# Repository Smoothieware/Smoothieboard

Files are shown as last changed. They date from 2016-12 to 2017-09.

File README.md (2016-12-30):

Smoothieboard
=============

Smoothieboard is a free, open source, high performance and modular G-code interpreter and CNC controller for the LPC17xx micro-controller (32-bit ARM Cortex-M3).

The current BoM (Bill of Materials) can be found at https://docs.google.com/spreadsheet/ccc?key=0Api7_ZbfikkKdGRDblUwMDFWcm1CT2M2bENkQWpZZ0E&usp=drive_web#gid=0

A separate list is maintained for the connectors at https://docs.google.com/spreadsheets/d/1bT7xw4z405cyhR7MyXegm4-C2oinxpVefuf3KV13v_A/edit#gid=0

Licensed under CERN OHL v.1.2 or later http://ohwr.org/cernohl
No warranty is provided for this documentation implied or otherwise.

The policy regarding third party "clones" and "derivatives" of Smoothieboard is found at http://smoothieware.org/policy

This documentation is hosted at http://github.com/Smoothieware/Smoothieboard

Firmware is found at http://github.com/Smoothieware/Smoothieware

Documentation of use is hosted on a wiki at http://smoothieware.org

For more info or to let us know what you are doing with Smoothie email wolf.arthur@gmail.com
or join the Smoothie community on IRC Freenode in #smoothieware http://smoothieware.org/irc

Smoothieware is a certified open source hardware project (UID FR000001).

Smoothieboard, and Smoothieware, and the Smoothie-namespace are all trademarks of The Smoothie Project.
The hardware and software of The Smoothie Project are licensed under the CERN OHL v1.2 or later and GPL v3 or later licensing agreements respectively.
Copyright 2011-2016 by Arthur Wolf and Mark Cooper

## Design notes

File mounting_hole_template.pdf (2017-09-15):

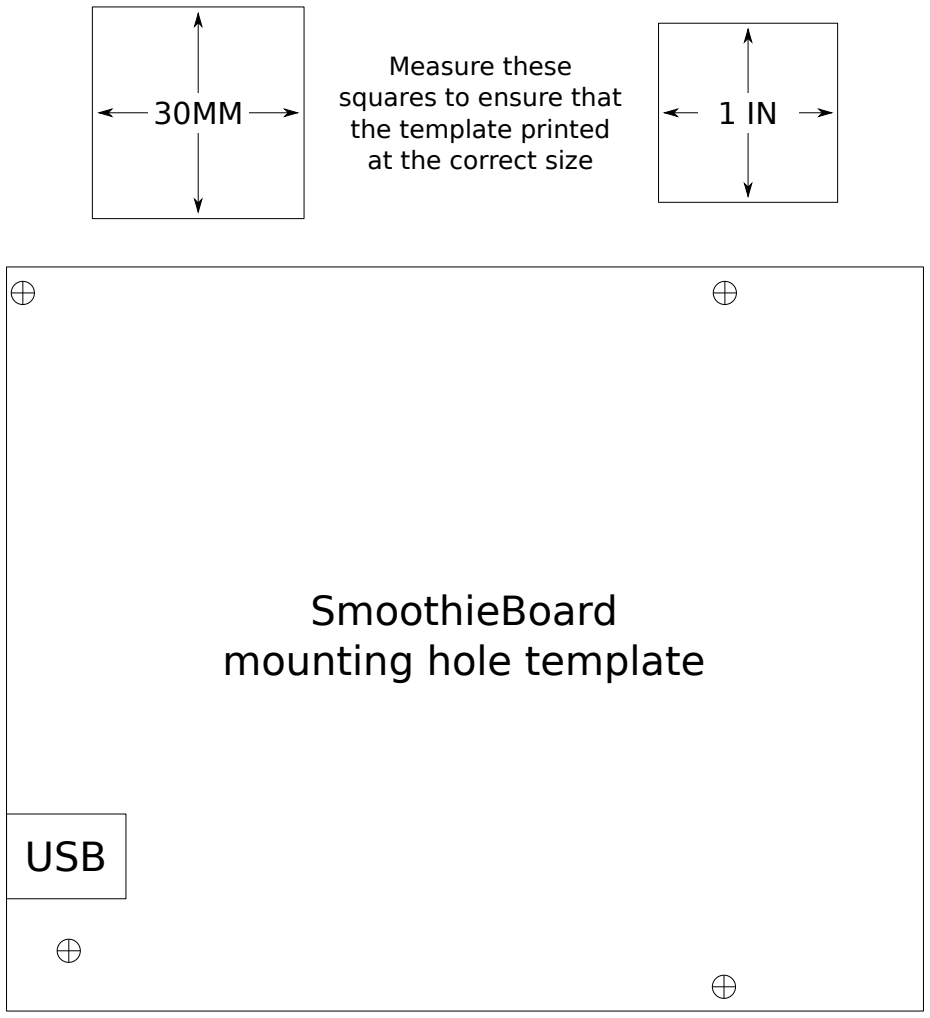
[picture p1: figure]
USB; SmoothieBoard mounting hole template; Measure these squares to ensure that the template printed at the correct size

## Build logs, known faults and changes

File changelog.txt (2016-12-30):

Smoothieboard Change Log

Smoothieboard v1.1 (2016/10)
 - upgraded stepper drivers to A5984 drivers with 32x microstepping
 - added a solder jumper (JP36) for MS3 on new A5984 drivers
 - changed the current limiting resistors (R78,R65-R68,R84-R85) for VBB powered LEDs to 8.2K
 - added an electrolytic capacitor (C84) to the 5V power system
 - moved the electrolytic capicitor (C63) for the 5x mosfet set and increased its footprint size
 - added flyback diodes (D7-D9) to small mosfet outputs to protect from inductive loads like small fans
 - added Open Source Hardware logo with UID (FR000001)

Smoothieboard v1.0b (2015/04)
 - reworked silkscreen adding reference ids back in
 - moved VBB jumper for small mosfet pair to increase room around C63
 - corrected the polarity of the zener diode in the VBB reverse polarity protection circuit
 - moved 5v reg backflow protection diode from the 5V side to the VBB side of the vreg
 - broke out AVCC and AGND to header
 - added solder jumper to TH4 passives

Smoothieboard v1.0a (2015/01)
 - update by Mark Cooper (Logxen)
 - reworked silkscreen with more pin numbers and without reference ids
 - added GND pin to the RST/ISP header
 - modified sdcard SPI1 header to match the pinout of the SPI0 header

Smoothieboard v1.0 (2014/09)
 - update by Mark Cooper (Logxen) and Michael Moon (Triffid_Hunter)
 - fixed missing connection between GND and AGND in KS layout
 - improved silkscreen
 - other small changes

Smoothieboard KS (2013/10)
 - expansion of the Beta design to a 5 driver layout by Michael Moon (Triffid_Hunter) and Mark Cooper (Logxen)
 - added "mixed" mosfet pair of one large and one small fet
 - improved VBB reverse polarity protection circuit
 - added esd protection to endstop circuits
 - added footprint for optional 5v regulator
 - additional GND pins for various headers
 - other small changes
 - produced by cooperation between Uberclock, Robotseed, and the Smoothie community
 - kickstarter page: https://www.kickstarter.com/projects/logxen/smoothieboard-the-future-of-cnc-motion-control

Smoothieboard Beta (2013/01)
 - designed by Arthur Wolf (arthur-_) and Eric Sorenson (ravix)
 - the original Smoothieboard Beta was a 4 stepper driver design
 - first produced by TrinityLabs and later produced by Ipsofactio which eventually rebranded as Robotseed
 - wiki page: http://smoothieware.org/smoothieboard-beta

Smoothieboard on a breadboard (circa 2011-current)
 - core design by Arthur Wolf (arthur-_)
 - original application circuits ported from RAMPS with modifications for use with 3.3V i/o
 - many community members built their own Smoothieboards on breadboards before Smoothieboards were commercially available
 - Smoothieboards on breadboards continue to be built today by people who are designing new derivative boards
 - wiki page: http://smoothieware.org/smoothie-on-a-breadboard

Smoothieboard and Smoothieware are trademarks of The Smoothie Project.
The hardware and software of The Smoothie Project are licensed under the CERN OHL v1.2 or later and GPL v3 or later licensing agreements respectively.
Copyright 2011-2016 by Arthur Wolf and Mark Cooper

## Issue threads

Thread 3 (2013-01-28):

2x3 connectors for ribbon cables ( SPI port ).

arthurwolf, 2013-01-28:
Hi !

I bought a bunch of these : http://www.ebay.com/itm/330833147832?ssPageName=STRK:MEWNX:IT&_trksid=p3984.m1497.l2649
They work great for the 5th-stepper connector, but a few caps and resistors are in the way for the SPI port. Could we move them away a bit ? ( that's on the beta board I have, may be different on the current eagle files ).
The connectors are 15*9mm.

Thanks !

Closed 2016-10-20.

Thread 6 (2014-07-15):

Menu typesetting messed up issue

zebrajack, 2014-07-15:
hi,
We use st7565_glcd for menu display, and the resolution is 128*64.After tedious configuration , finally it works, but the menu typesetting is a big issue as the following:

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

As we can see the first row is right typesetting when it is intialized, but it will change from time to time, switch back and force from 3 rows.

Does anyone encounter the same issue? Any suggestion are welcome!

Regards!
Cheng

Closed 2016-10-20.

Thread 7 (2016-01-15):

Stuck thermistors

traverseda, 2016-01-15:
Not sure exactly what happened, but the smoothieboard released a big puff of smoke, and the thermistors *stuck*. At 22.3 and 17.7 respectively.

Thankfully we were doing maintenance, and it didn't light anything on fire.

Looks like it was the chip next to c41. I'm guessing a A4982SLPTR-T.

Rebooted and the thermistors unstuck. Still pretty unclear on exactly what happened. Best guess is that it shorted on *something*, but whatever it was we can't find it.

Anyway, it's worth noting that the thermistors can fail partially open.

Closed 2016-10-20.

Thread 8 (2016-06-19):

R78 is too small

Zaaphod, 2016-06-19:
This is just a suggestion for a minor improvement to smoothieboard.  I recently hooked up my smoothieboard to a 24V power supply and noticed immediately that the red VBB led was so bright I could hardly see the nearby green led's 1-4

R78 is too small in comparison to the other current limiting resistors.  This is the current limiting resistor on the VBB LED10.  It's 2.2Kohms, but even at 12V the LED is extremely bright in comparison to the other LEDs,  and at 24V it's extremely bright.  The 2.2K resistor on LED 10 would make it draw 4.6mA at 12V and 10mA at 24V,  this is completely out or range of the other LEDs that draw only 1.5mA with their 1K current limiting resistors and 3.3V sources.

I noticed that other LEDs powered by VBB such as  LED5 - LED8 on the output FETs are 5.6K.  This is more in range if VBB=12V as the LED would be limited to 1.8mA  however at 24V it would still be overpowering at 4mA.
I would suggest 6.8Kohm - 10Kohm resistors for R78, and R65-R68 This would provide 1.5ma (6.8K) to 1mA (10K) at 12V and 3.3mA(6.8k) to 2.2mA(10k) at 24V - keeping these much more in range with the other LEDs.  Since I personally prefer 24V I would lean toward 10K, however even with 6.8K it would be much more in range of the other LEDs

Another option would be to make R78 5.6K and keep R65-R68 as is at 5.6K but then also reduce the size R10-R13 to 500-820ohms, this would make the green led's a little brighter. I would leave R77 alone because it's fine the way it is and is already brighter than the green LEDs

I realize this is a minor detail, but smoothie should be as good as it can be, and it's also a simple change to make.. no changes need to be made other than to change the resistor values.

Just for reference, I'm using 1.8v for the LED voltage drop and the formula  I=V-1.8/R  I don't know the exact specification of the LED's used

logxen, 2016-06-26:
Yeah, this has actually been bothering me for quite a while. I should make all of the VBB based resistors match in the next board revision.

  Your suggestion of 10K is a nice compromise between the two standard voltages used. I want to avoid using that specific value though because it is potentially confusing. The value of 10K strongly implies that the part is a simple pull-up or pull-down. The nearest values in the 10% series are 8.2K and 12K. I think 8.2K would be a good choice. Any higher than 10K and I fear the VBB leds would appear visibly dim at 12V.

Zaaphod, 2016-06-26:
I don't see what difference it makes whether it is the same value as a pull-up resistor, it's obviously in series with the LED.  However 8.2K would be way more balanced than the 2.2K resistor that is in there and be a big improvement.   If you wanted to stay away from 10K, then perhaps go with 8.2K for VBB resistors then decrease the green LED resistors to maybe 680ohms to help brighten the green LEDs a little.

logxen, 2016-11-06:
Being addressed in v1.1

Closed 2016-11-06.

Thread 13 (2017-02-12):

version updates missing

analogmonster, 2017-02-12:
eagle files still say v1.0 in the bottom right on schematic page - see page 3 of pdf and eagle sch.  Also may I suggest v1.1 be added to all pages.  I was looking for D7/D8 on my v1.0b board until I realised there was a misprint within eagle and I was referring to the wrong schematic

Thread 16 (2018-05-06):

Schematic file

seaghdh, 2018-05-06:
The .sch file is damaged. I want a .sch schema file.

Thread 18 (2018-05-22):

Add dimensions?

myk3y, 2018-05-22:
Nice to see a printable template for the board - would it be possible to put the dimensions and mount points in x,y format on the pdf?

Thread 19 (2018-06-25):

missing images in documentation

Jorgininho, 2018-06-25:
Hello,
I'm trying to follow the documentation on install smoothie on a k40 bluebox, but the images are not present in the both page
http://smoothieware.org/blue-box-guide
and
http://smoothieware.org/bluebox-guide

I remember there were usefull info on the type of alimentation of the laser and how to connect it

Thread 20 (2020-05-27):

Next rev:  room for friction locks on header connectors

MisterScott, 2020-05-27:
In the next revision, please position the 0.1" header connectors and surrounding components to allow use of friction lock style connectors.  An example 4-pin P/N is Molex 22-16-2041.
Planning to use my Smoothieboard in a CNC mill and I expect vibration; I would appreciate the assurance that connectors will not work loose over time that is provided by locking ramps.

arthurwolf, 2020-05-27:
I have seen users fit locking connectors in the current footprints. I don't
have the part numbers in mind though.

On Wed, May 27, 2020 at 10:34 PM MisterScott <notifications@github.com>
wrote:

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

--

勇気とユーモア

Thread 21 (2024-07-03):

Fails when connecting heater cartridge

Tinchus2009, 2024-07-03:
Hello. I have an old smoothoeboard, verson 1 may be?
Iwas working ok but a heater cartridge failed last week. I though the heater cartridge failed so I replaced it but the new one didnt worked. First thing I did was removing and disconecting the cartridge, turned upside down my printer and check the board, all lights looked ok. I turned on the heater and I can see the oboard led (big mosfet q7 I think it is called) ON. I checked the voltage and I can read 12.5 V there.

Soi I connect the new heater cartridge, turn on everything again. LED on the board is on, but I checked voltage on the conector and now there is no voltage there.

So my guess there is some problem on the board?

May be this component is wrong?

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

Please help me

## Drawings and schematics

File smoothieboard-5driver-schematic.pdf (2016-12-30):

A

A

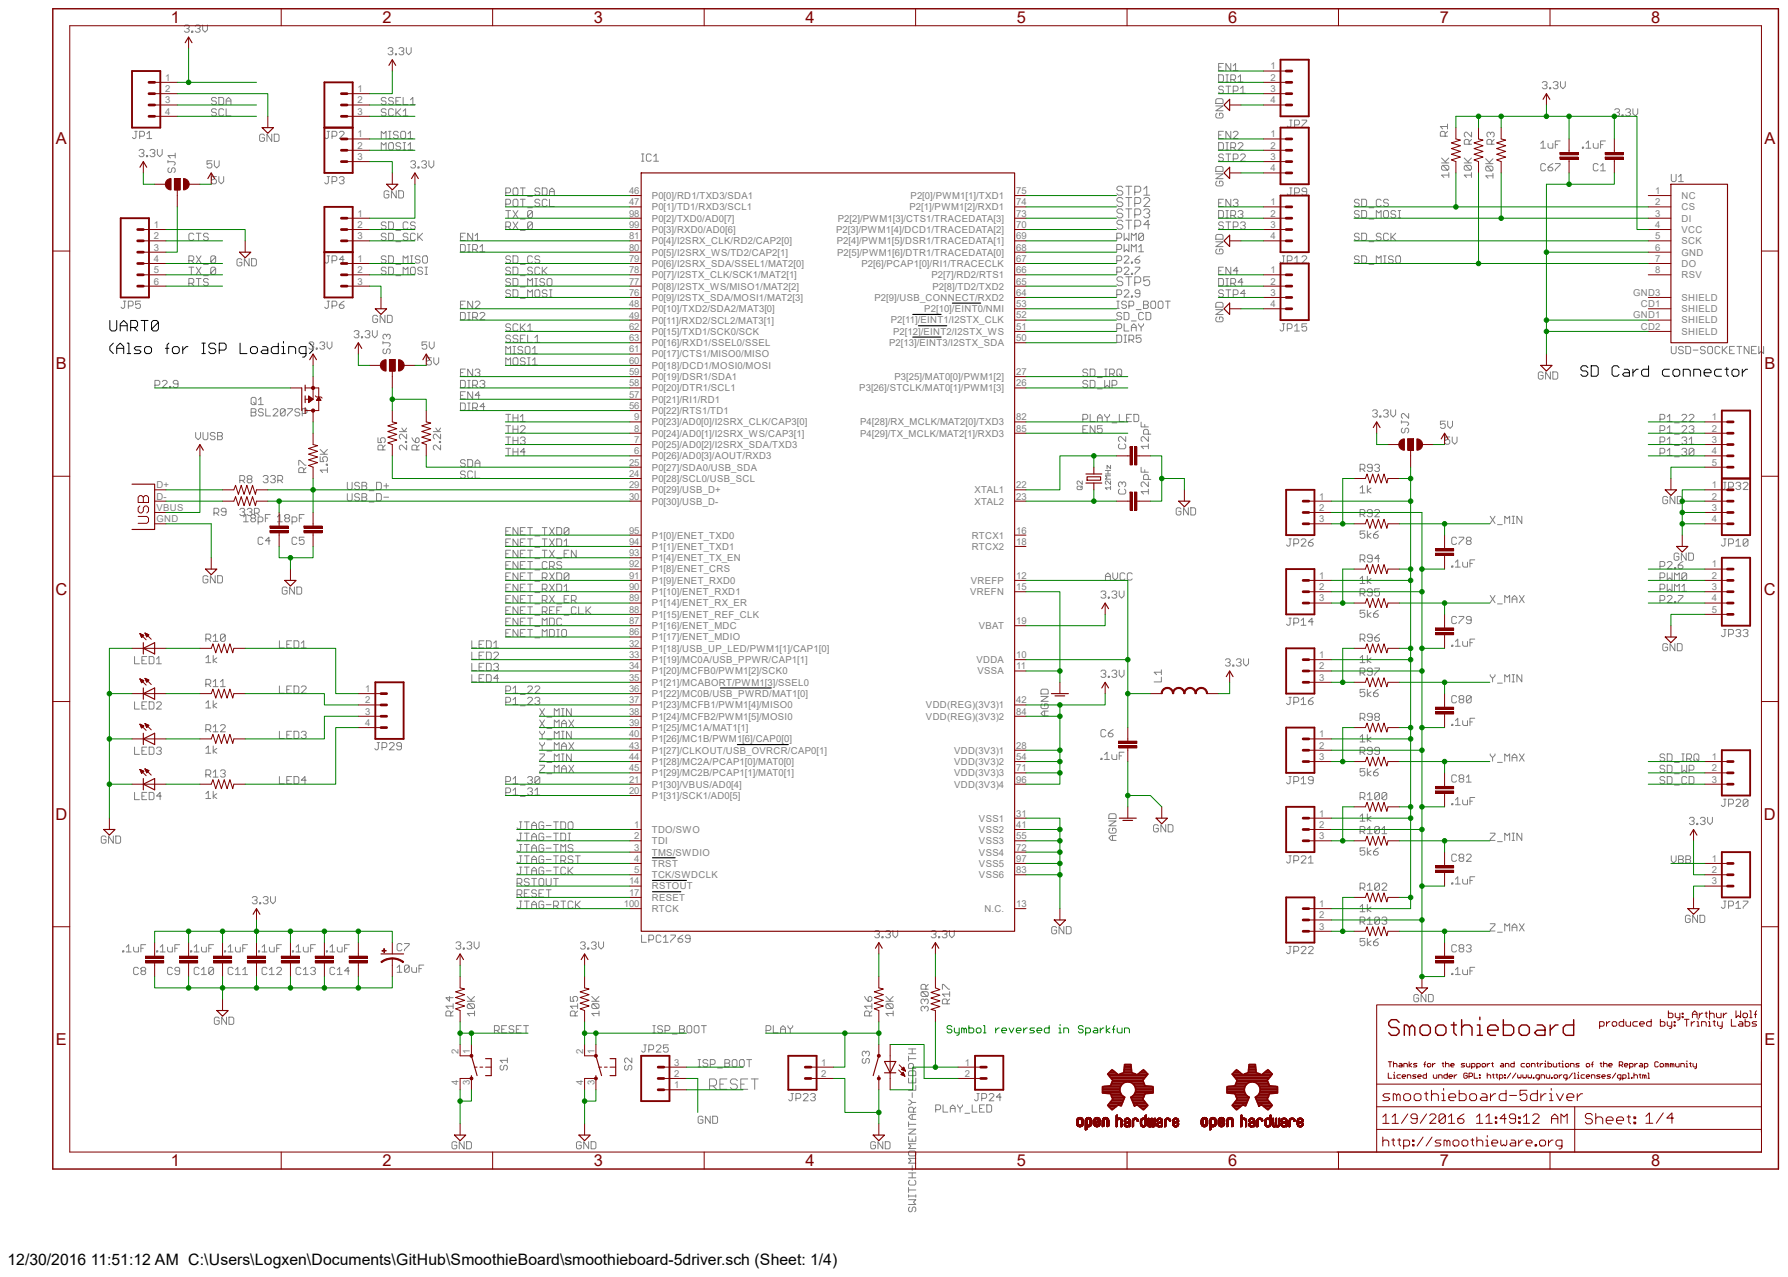
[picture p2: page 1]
TDO/SWO 1 TDI 2 TMS/SWDIO 3 TRST 4 TCK/SWDCLK 5; P0[26]/AD0[3]/AOUT/RXD3 6 P0[25]/AD0[2]/I2SRX_SDA/TXD3 7 P0[24]/AD0[1]/I2SRX_WS/CAP3[1] 8 P0[23]/AD0[0]/I2SRX_CLK/CAP3[0] 9; VDDA 10 VSSA 11; VREFP 12; RSTOUT 14; VREFN 15; RTCX1 16; RESET 17; RTCX2 18; VBAT 19; P1[31]/SCK1/AD0[5] 20 P1[30]/VBUS/AD0[4] 21; XTAL1 22 XTAL2 23; P0[28]/SCL0/USB_SCL 24 P0[27]/SDA0/USB_SDA 25; P3[26]/STCLK/MAT0[1]/PWM1[3] 26 P3[25]/MAT0[0]/PWM1[2] 27; VDD(3V3)1 28; P0[29]/USB_D+ 29 P0[30]/USB_D- 30; VSS1 31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

P2[9]/USB_CONNECT/RXD2 64 P2[8]/TD2/TXD2 65 P2[7]/RD2/RTS1 66 P2[6]/PCAP1[0]/RI1/TRACECLK 67 P2[5]/PWM1[6]/DTR1/TRACEDATA[0] 68 P2[4]/PWM1[5]/DSR1/TRACEDATA[1] 69 P2[3]/PWM1[4]/DCD1/TRACEDATA[2] 70

12/30/2016 11:51:12 AM C:\Users\Logxen\Documents\GitHub\SmoothieBoard\smoothieboard-5driver.sch (Sheet: 1/4)

A

A

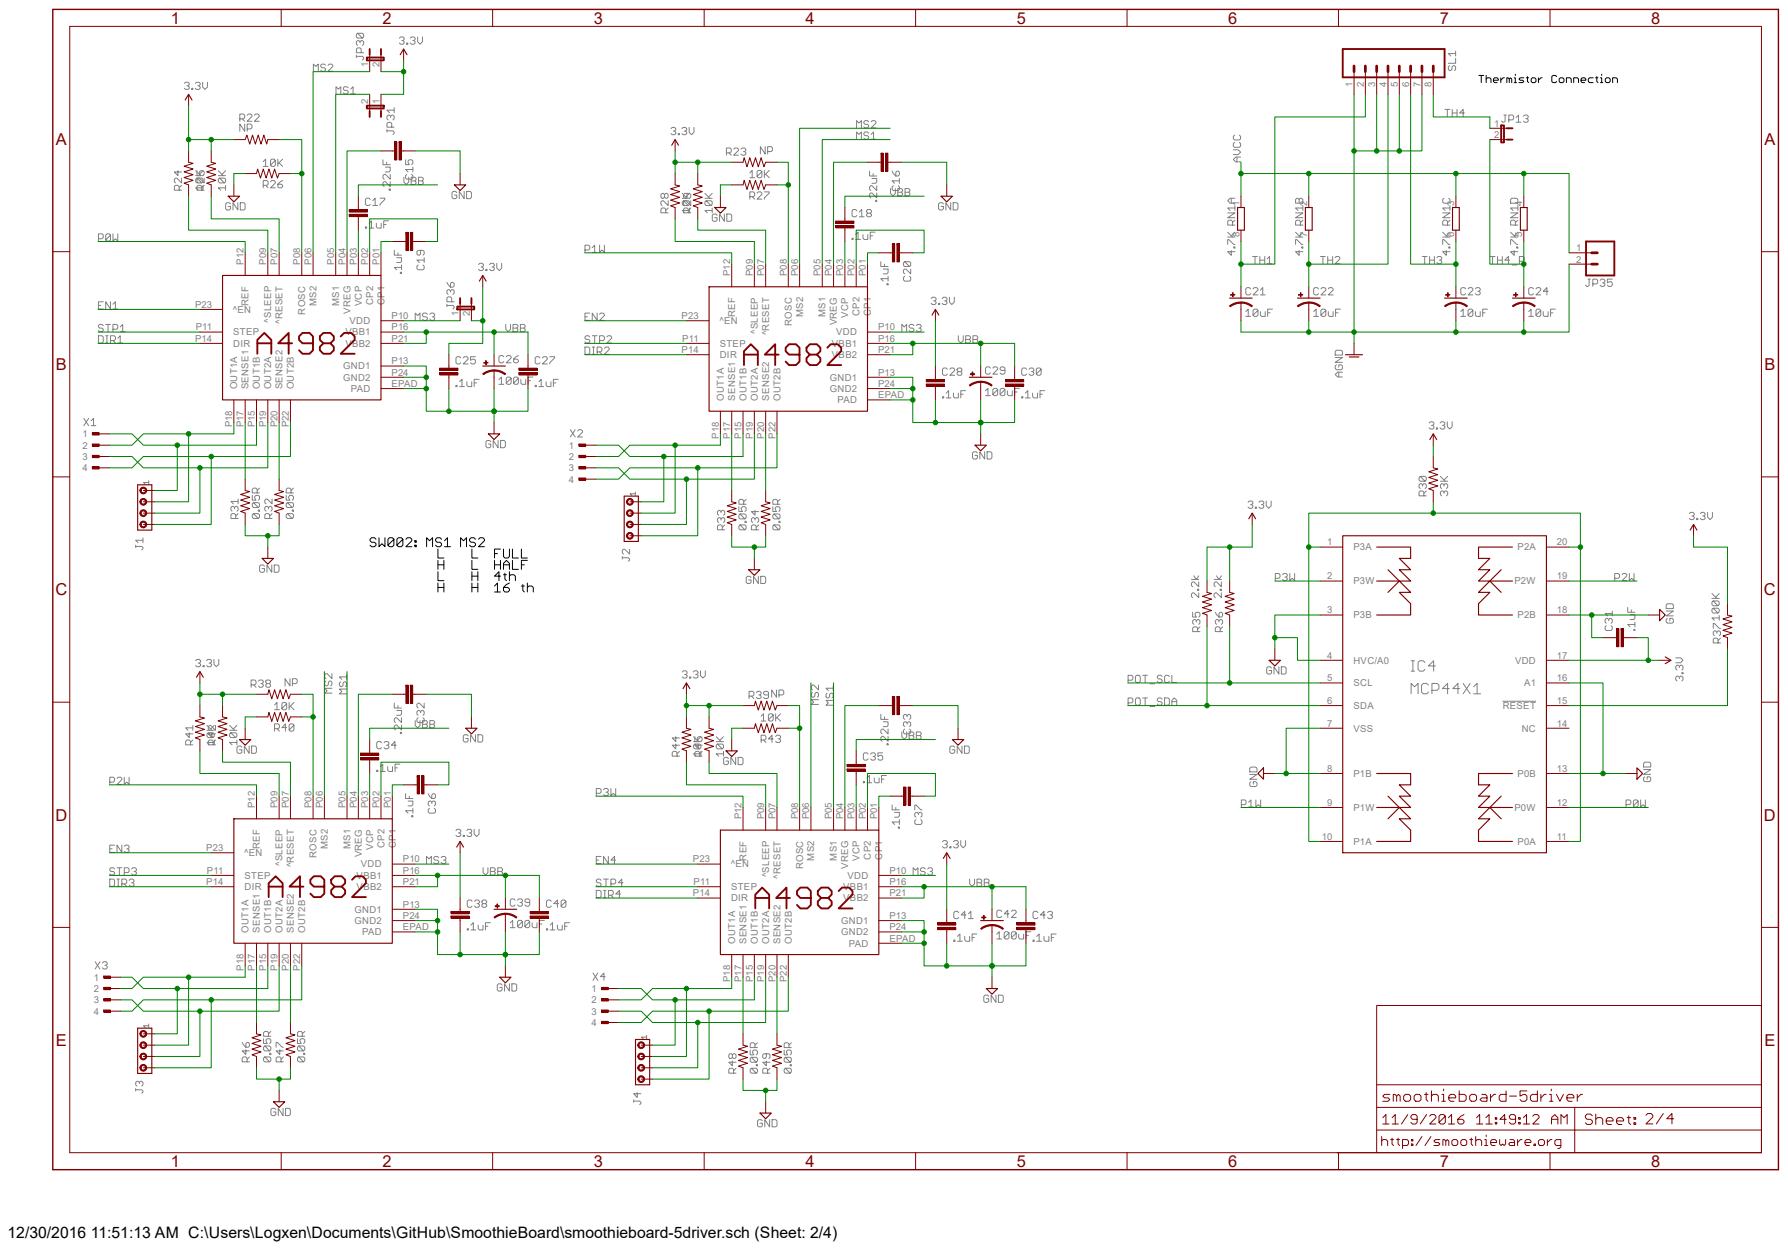
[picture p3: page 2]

12/30/2016 11:51:13 AM C:\Users\Logxen\Documents\GitHub\SmoothieBoard\smoothieboard-5driver.sch (Sheet: 2/4)

A

A

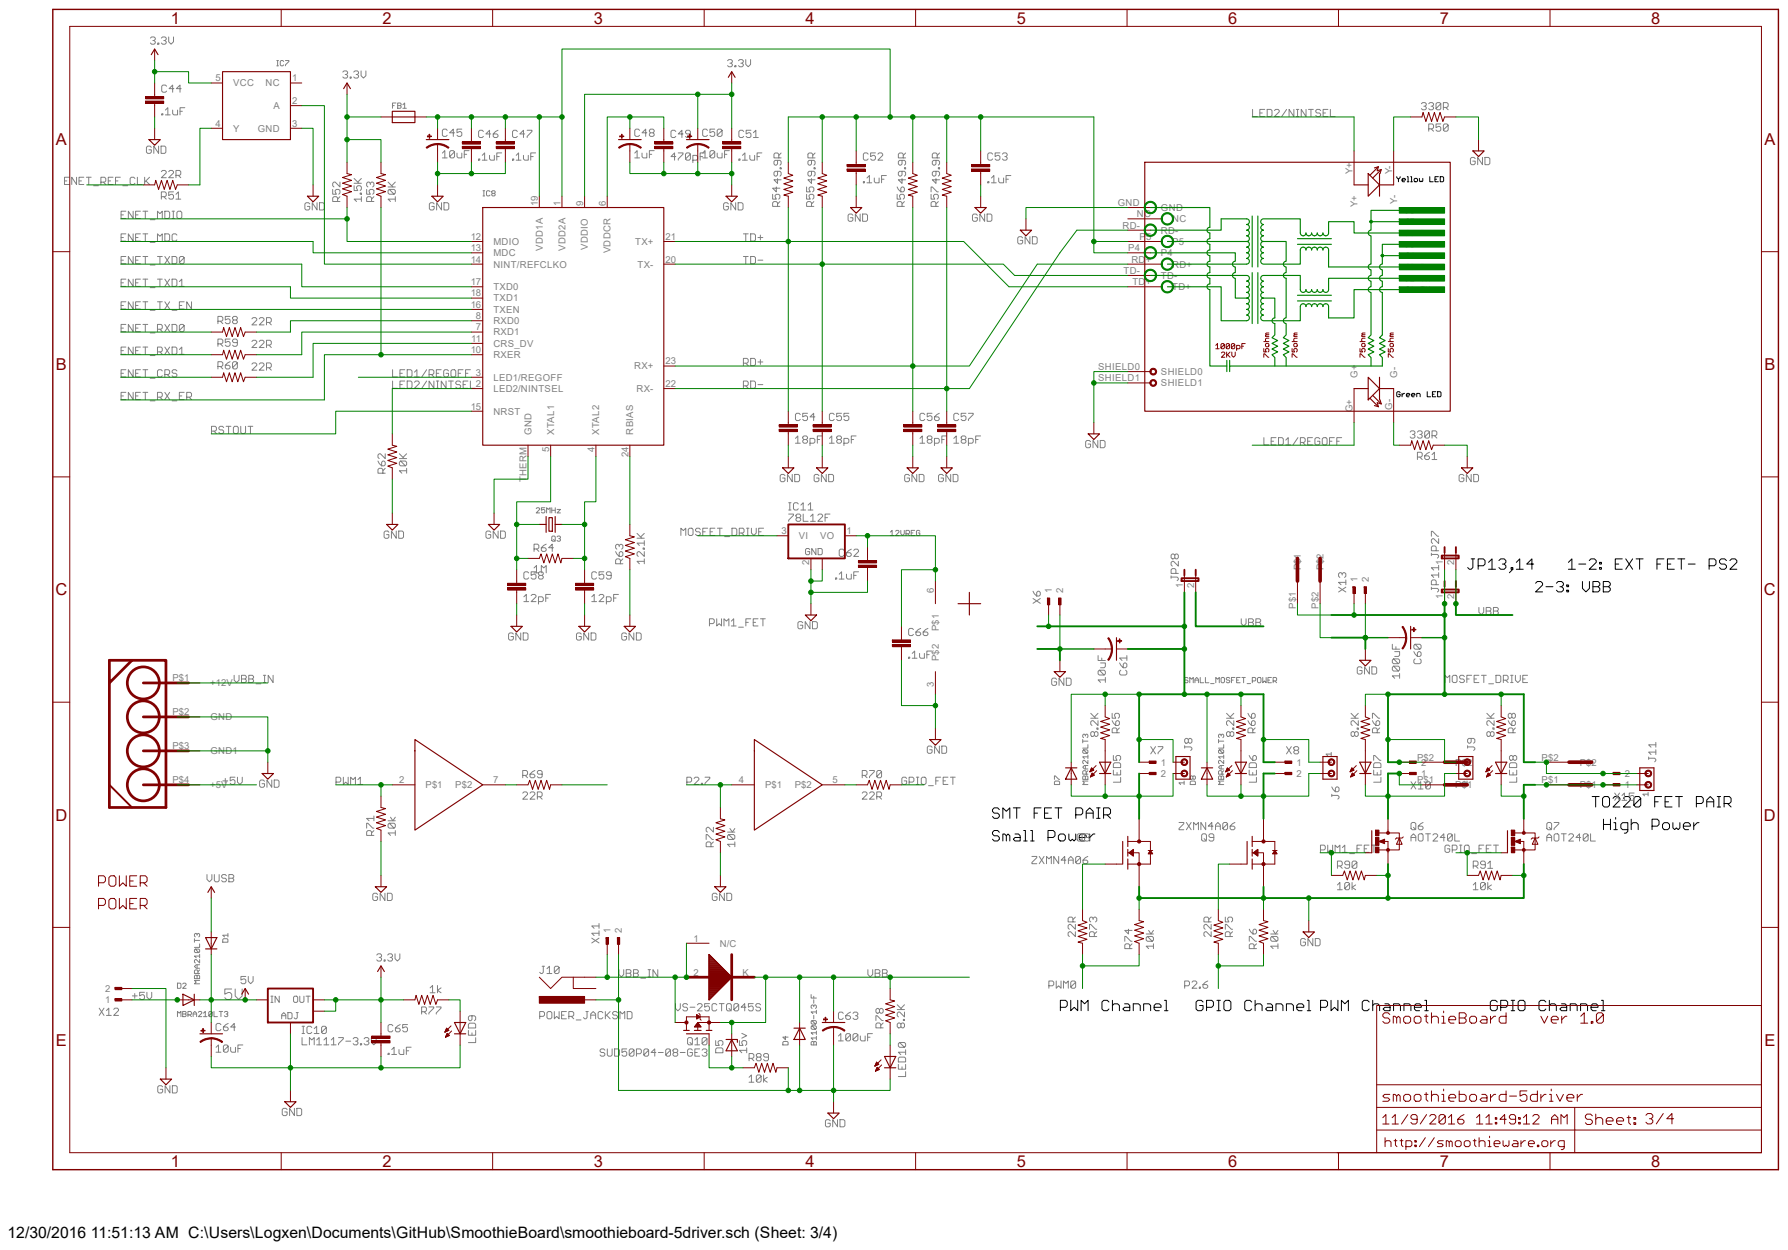
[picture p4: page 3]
MDIO 12 MDC 13 NINT/REFCLKO 14; TXD0 17 TXD1 18 TXEN 16 RXD0 8 RXD1 7; RXER 10; LED1/REGOFF 3 LED2/NINTSEL 2; NRST 15; XTAL1; XTAL2; CRS_DV 11; RBIAS 24; GND THERM; VDD1A 19; VDD2A; VDDIO; VDDCR; GND 3 Y 4; VCC 5; GND P$2; GND1 P$3; SHIELD0 SHIELD0 SHIELD1 SHIELD1

GND

12/30/2016 11:51:13 AM C:\Users\Logxen\Documents\GitHub\SmoothieBoard\smoothieboard-5driver.sch (Sheet: 3/4)

A

A

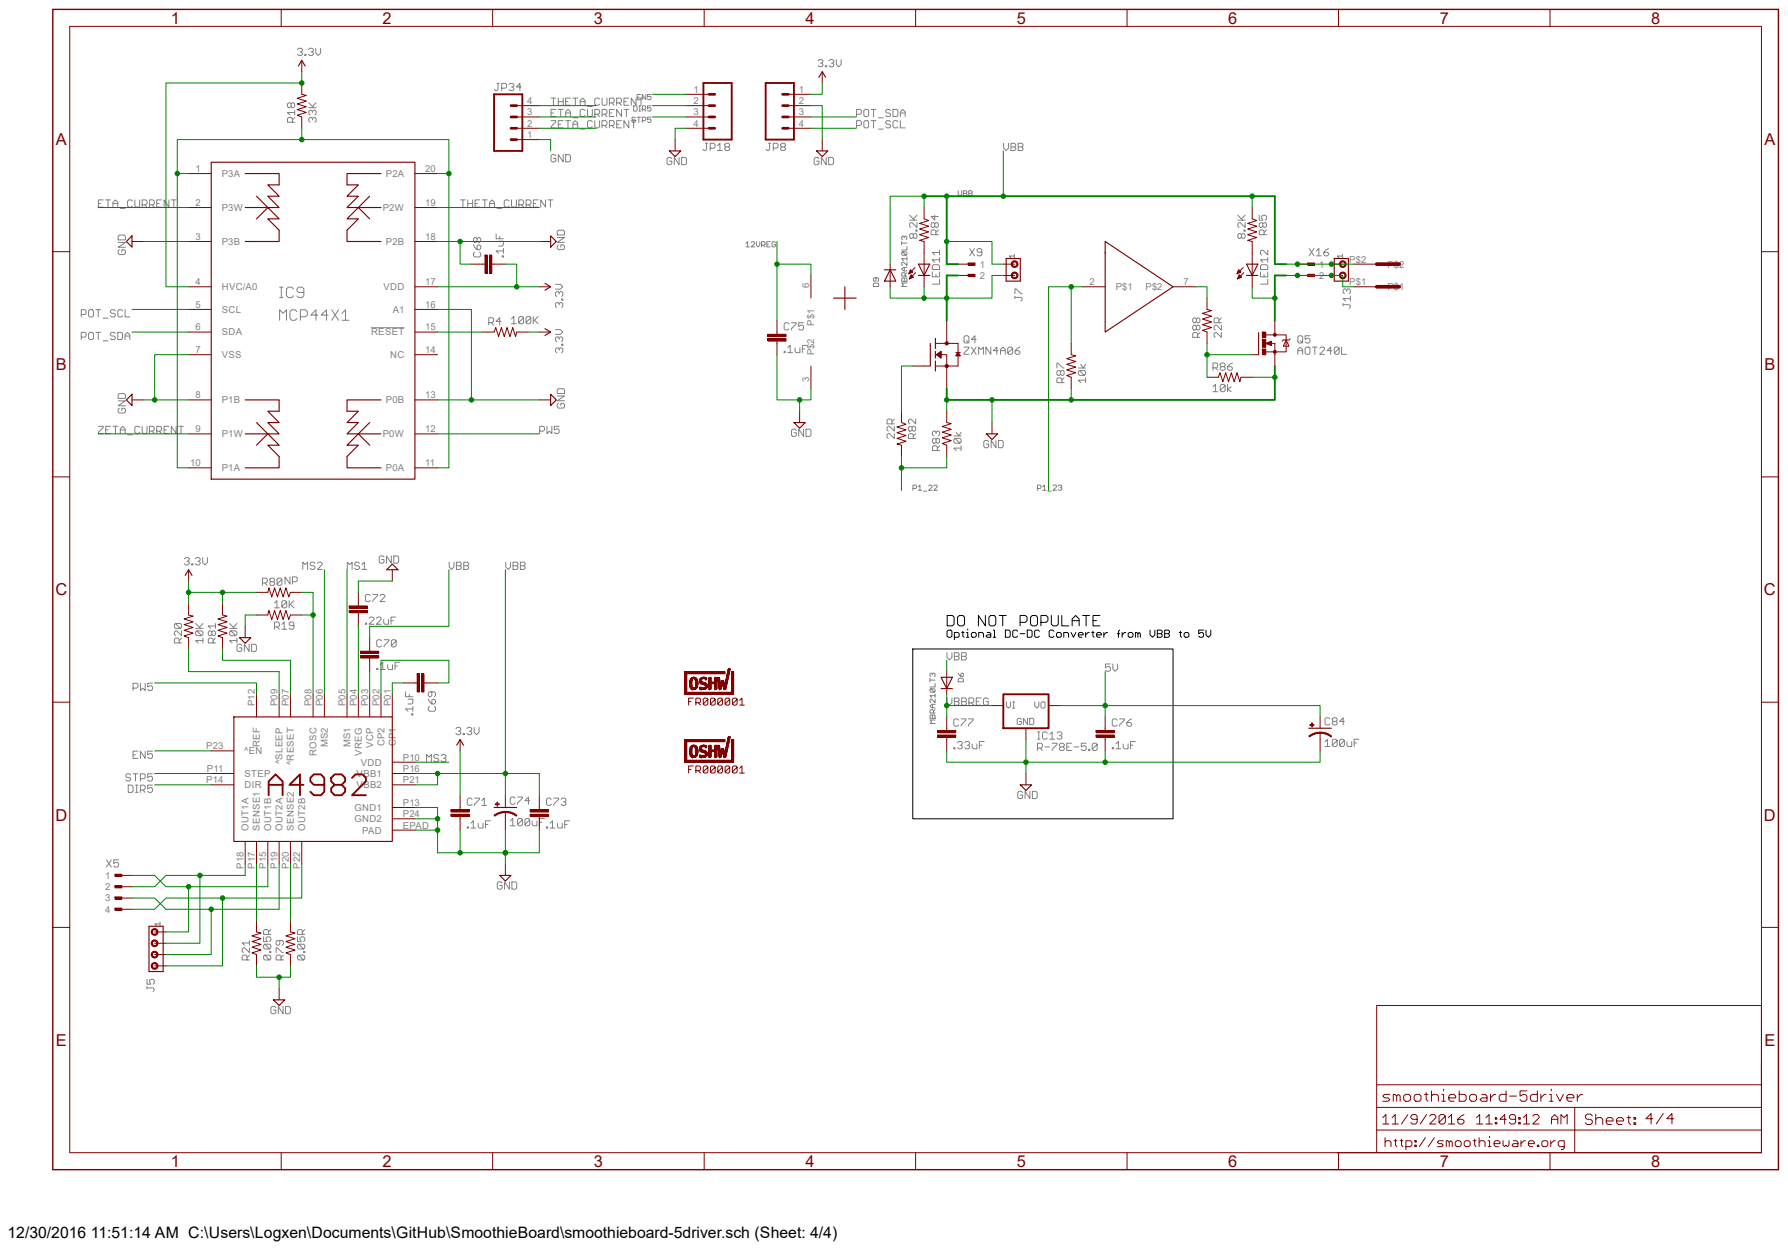
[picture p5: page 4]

12/30/2016 11:51:14 AM C:\Users\Logxen\Documents\GitHub\SmoothieBoard\smoothieboard-5driver.sch (Sheet: 4/4)

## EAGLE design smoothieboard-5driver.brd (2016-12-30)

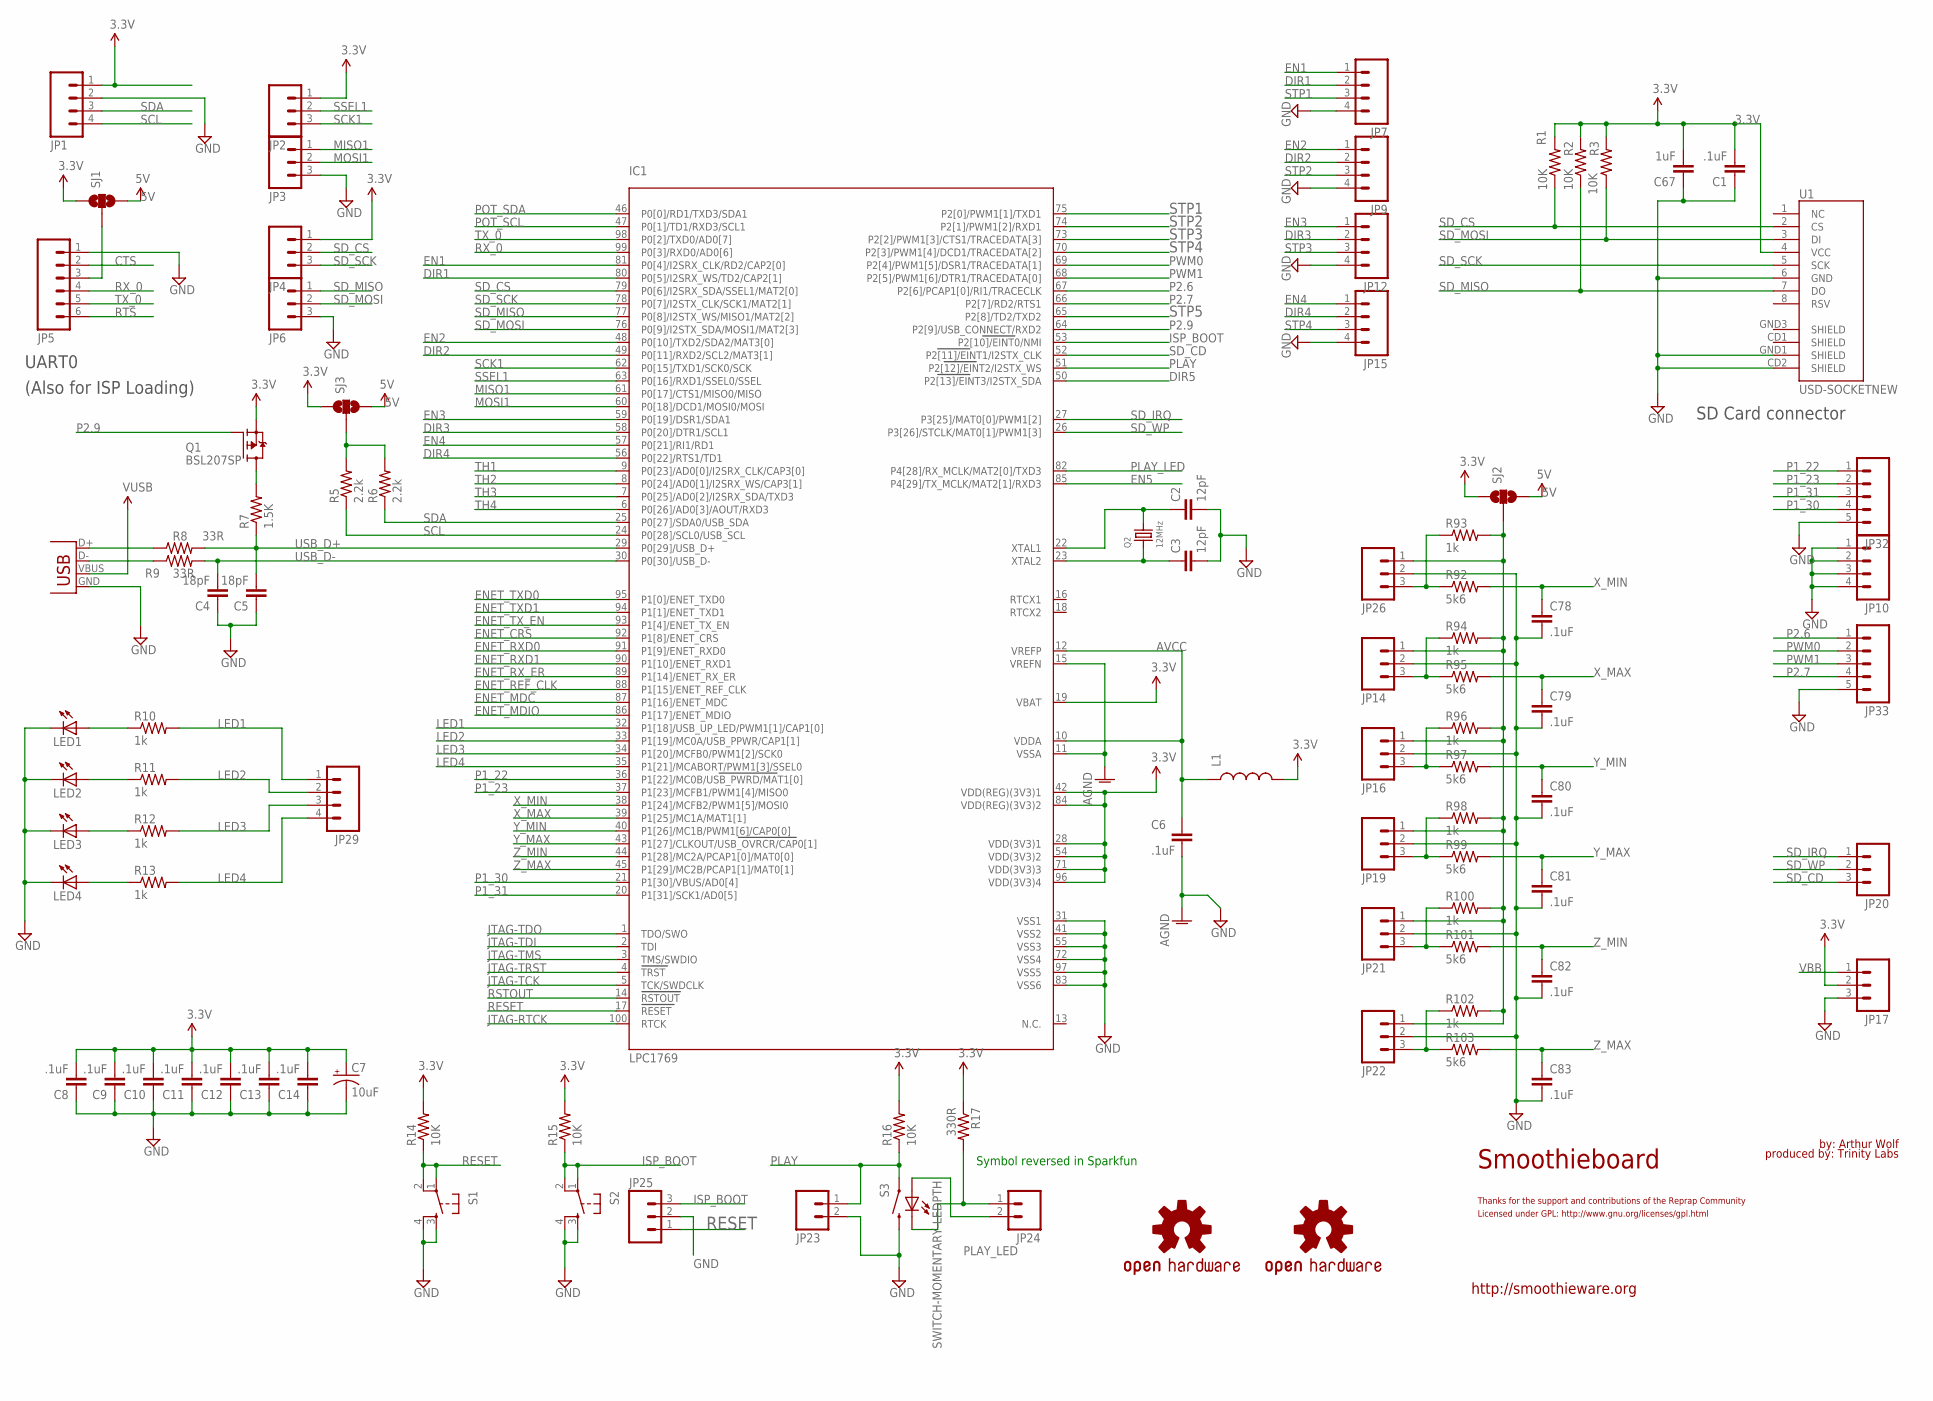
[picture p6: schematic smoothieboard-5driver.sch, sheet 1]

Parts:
C1, C6, C8, C9, C10, C11, C12, C13, C14, C78, C79, C80, C81, C82, C83: .1uF; C0603
C2, C3: 12pF; C0603
C4, C5: 18pF; C0603
C7: 10uF; EIA3216
C67: 1uF; C0805
IC1: LPC1769; LQFP100
JP1, JP7, JP9, JP10, JP12, JP15, JP29: M041X04_NO_SILK; 1X04_NO_SILK
JP2, JP3, JP4, JP6: M031X03_NO_SILK; 1X03_NO_SILK
JP5: M06POLAR; MOLEX-1X6
JP14, JP16, JP19, JP21, JP22, JP26: M03POLAR; MOLEX-1X3
JP17, JP20, JP25: M03PTH; 1X03
JP23, JP24: M02PTH; 1X02
JP32, JP33: M05PTH; 1X05
L1: INDUCTOR0603; 0603
LED1, LED2, LED3, LED4: LEDCHIP-LED0805; CHIP-LED0805
Q1: BSL207SP; SC74_INFINEON
Q2: 12MHz; CRYSTAL_3.2X2.5
R1, R2, R3, R14, R15, R16: 10K; R0603
R5, R6: 2.2k; R0603
R7: 1.5K; R0603
R8, R9: 33R; R0603
R10, R11, R12, R13, R93, R94, R96, R98, R100, R102: 1k; R0603
R17: 330R; R0603
R92, R95, R97, R99, R101, R103: 5k6; R0603
S1, S2: TAC_SWITCHSMD; TACTILE_SWITCH_SMD
S3: SWITCH-MOMENTARY-LEDPTH; TACTILE-PTH-LED-12MM
SJ1, SJ2, SJ3: SOLDERJUMPER_2WAYS; SJ_3
U1: USD-SOCKETNEW; MICRO-SD-SOCKET-PP
U$8, U$9: OSHW-LOGOH; OSHW-LOGO-HUGE
X14: USBPTH; USB-B-PTH

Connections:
3.3V: C1.2, C7.A (+), C8.2, C9.2, C10.2, C11.2, C12.2, C13.2, C14.2, C67.2, IC1.19 (VBAT), IC1.28 (VDD(3V3)1), IC1.42 (VDD(REG)(3V3)1), IC1.54 (VDD(3V3)2), IC1.71 (VDD(3V3)3), IC1.84 (VDD(REG)(3V3)2), IC1.96 (VDD(3V3)4), JP1.1, JP2.1, JP4.1, JP17.2, L1.2, Q1.4 (S), R1.2, R2.2, R3.2, R14.2, R15.2, R16.2, R17.1, SJ1.1, SJ2.1, SJ3.1, U1.4 (VCC); also elsewhere on the board
5V: SJ1.3, SJ2.3, SJ3.3; also elsewhere on the board
AGND: C6.2, IC1.11 (VSSA), IC1.15 (VREFN); also elsewhere on the board
AVCC: C6.1, IC1.10 (VDDA), IC1.12 (VREFP), L1.1; also elsewhere on the board
CTS: JP5.2
DIR1: IC1.80 (P0[5]/I2SRX_WS/TD2/CAP2[1]), JP7.2; also elsewhere on the board
DIR2: IC1.49 (P0[11]/RXD2/SCL2/MAT3[1]), JP9.2; also elsewhere on the board
DIR3: IC1.58 (P0[20]/DTR1/SCL1), JP12.2; also elsewhere on the board
DIR4: IC1.56 (P0[22]/RTS1/TD1), JP15.2; also elsewhere on the board
DIR5: IC1.50 (P2[13]/EINT3/I2STX_SDA); also elsewhere on the board
EN1: IC1.81 (P0[4]/I2SRX_CLK/RD2/CAP2[0]), JP7.1; also elsewhere on the board
EN2: IC1.48 (P0[10]/TXD2/SDA2/MAT3[0]), JP9.1; also elsewhere on the board
EN3: IC1.59 (P0[19]/DSR1/SDA1), JP12.1; also elsewhere on the board
EN4: IC1.57 (P0[21]/RI1/RD1), JP15.1; also elsewhere on the board
EN5: IC1.85 (P4[29]/TX_MCLK/MAT2[1]/RXD3); also elsewhere on the board
ENET_CRS: IC1.92 (P1[8]/ENET_CRS); also elsewhere on the board
ENET_MDC: IC1.87 (P1[16]/ENET_MDC); also elsewhere on the board
ENET_MDIO: IC1.86 (P1[17]/ENET_MDIO); also elsewhere on the board
ENET_REF_CLK: IC1.88 (P1[15]/ENET_REF_CLK); also elsewhere on the board
ENET_RXD0: IC1.91 (P1[9]/ENET_RXD0); also elsewhere on the board
ENET_RXD1: IC1.90 (P1[10]/ENET_RXD1); also elsewhere on the board
ENET_RX_ER: IC1.89 (P1[14]/ENET_RX_ER); also elsewhere on the board
ENET_TXD0: IC1.95 (P1[0]/ENET_TXD0); also elsewhere on the board
ENET_TXD1: IC1.94 (P1[1]/ENET_TXD1); also elsewhere on the board
ENET_TX_EN: IC1.93 (P1[4]/ENET_TX_EN); also elsewhere on the board
GND: C1.1, C2.2, C3.2, C4.1, C5.1, C7.C (-), C8.1, C9.1, C10.1, C11.1, C12.1, C13.1, C14.1, C67.1, C78.2, C79.2, C80.2, C81.2, C82.2, C83.2, IC1.31 (VSS1), IC1.41 (VSS2), IC1.55 (VSS3), IC1.72 (VSS4), IC1.83 (VSS6), IC1.97 (VSS5), JP1.2, JP3.3, JP5.1, JP6.3, JP7.4, JP9.4, JP10.1, JP10.2, JP10.3, JP10.4, JP12.4, JP14.2, JP15.4, JP16.2, JP17.3, JP19.2, JP21.2, JP22.2, JP23.2, JP25.2, JP26.2, JP32.5, JP33.5, LED1.C, LED2.C, LED3.C, LED4.C, S1.3, S1.4, S2.3, S2.4, S3.2, U1.6 (GND), U1.CD2 (SHIELD), U1.GND1 (SHIELD), X14.GND; also elsewhere on the board
ISP_BOOT: IC1.53 (P2[10]/EINT0/NMI), JP25.3, R15.1, S2.1, S2.2
JTAG-RTCK: IC1.100 (RTCK)
JTAG-TCK: IC1.5 (TCK/SWDCLK)
JTAG-TDI: IC1.2 (TDI)
JTAG-TDO: IC1.1 (TDO/SWO)
JTAG-TMS: IC1.3 (TMS/SWDIO)
JTAG-TRST: IC1.4 (TRST)
LED1: IC1.32 (P1[18]/USB_UP_LED/PWM1[1]/CAP1[0]), JP29.1, R10.2
LED2: IC1.33 (P1[19]/MC0A/USB_PPWR/CAP1[1]), JP29.2, R11.2
LED3: IC1.34 (P1[20]/MCFB0/PWM1[2]/SCK0), JP29.3, R12.2
LED4: IC1.35 (P1[21]/MCABORT/PWM1[3]/SSEL0), JP29.4, R13.2
MISO1: IC1.61 (P0[17]/CTS1/MISO0/MISO), JP3.1
MOSI1: IC1.60 (P0[18]/DCD1/MOSI0/MOSI), JP3.2
unnamed: C2.1, IC1.22 (XTAL1), Q2.2
unnamed: C3.1, IC1.23 (XTAL2), Q2.1
unnamed: JP5.3, SJ1.2
unnamed: Q1.1 (D), Q1.2 (D), Q1.5 (D), Q1.6 (D), R7.2
unnamed: R8.1, X14.D+
unnamed: R9.1, X14.D-
unnamed: JP24.1, R17.2, S3.C
unnamed: LED4.A, R13.1
unnamed: LED3.A, R12.1
unnamed: LED2.A, R11.1
unnamed: LED1.A, R10.1
unnamed: JP14.3, R94.1, R95.1
unnamed: JP14.1, JP16.1, JP19.1, JP21.1, JP22.1, JP26.1, R93.2, R94.2, R96.2, R98.2, R100.2, R102.2, SJ2.2
unnamed: JP16.3, R96.1, R97.1
unnamed: JP19.3, R98.1, R99.1
unnamed: JP22.3, R102.1, R103.1
unnamed: JP21.3, R100.1, R101.1
unnamed: JP26.3, R92.1, R93.1
unnamed: R5.2, R6.2, SJ3.2
P1_22: IC1.36 (P1[22]/MC0B/USB_PWRD/MAT1[0]), JP32.1; also elsewhere on the board
P1_23: IC1.37 (P1[23]/MCFB1/PWM1[4]/MISO0), JP32.2; also elsewhere on the board
P1_30: IC1.21 (P1[30]/VBUS/AD0[4]), JP32.4
P1_31: IC1.20 (P1[31]/SCK1/AD0[5]), JP32.3
P2.6: IC1.67 (P2[6]/PCAP1[0]/RI1/TRACECLK), JP33.1; also elsewhere on the board
P2.7: IC1.66 (P2[7]/RD2/RTS1), JP33.4; also elsewhere on the board
P2.9: IC1.64 (P2[9]/USB_CONNECT/RXD2), Q1.3 (G)
PLAY: IC1.51 (P2[12]/EINT2/I2STX_WS), JP23.1, R16.1, S3.4 (1)
PLAY_LED: IC1.82 (P4[28]/RX_MCLK/MAT2[0]/TXD3), JP24.2, S3.A
POT_SCL: IC1.47 (P0[1]/TD1/RXD3/SCL1); also elsewhere on the board
POT_SDA: IC1.46 (P0[0]/RD1/TXD3/SDA1); also elsewhere on the board
PWM0: IC1.69 (P2[4]/PWM1[5]/DSR1/TRACEDATA[1]), JP33.2; also elsewhere on the board
PWM1: IC1.68 (P2[5]/PWM1[6]/DTR1/TRACEDATA[0]), JP33.3; also elsewhere on the board
RESET: IC1.17 (RESET), JP25.1, R14.1, S1.1, S1.2
RSTOUT: IC1.14 (RSTOUT); also elsewhere on the board
RTS: JP5.6
RX_0: IC1.99 (P0[3]/RXD0/AD0[6]), JP5.4
SCK1: IC1.62 (P0[15]/TXD1/SCK0/SCK), JP2.3
SCL: IC1.24 (P0[28]/SCL0/USB_SCL), JP1.4, R5.1
SDA: IC1.25 (P0[27]/SDA0/USB_SDA), JP1.3, R6.1
SD_CD: IC1.52 (P2[11]/EINT1/I2STX_CLK), JP20.3
SD_CS: IC1.79 (P0[6]/I2SRX_SDA/SSEL1/MAT2[0]), JP4.2, R1.1, U1.2 (CS)
SD_IRQ: IC1.27 (P3[25]/MAT0[0]/PWM1[2]), JP20.1
SD_MISO: IC1.77 (P0[8]/I2STX_WS/MISO1/MAT2[2]), JP6.1, R2.1, U1.7 (DO)
SD_MOSI: IC1.76 (P0[9]/I2STX_SDA/MOSI1/MAT2[3]), JP6.2, R3.1, U1.3 (DI)
SD_SCK: IC1.78 (P0[7]/I2STX_CLK/SCK1/MAT2[1]), JP4.3, U1.5 (SCK)
SD_WP: IC1.26 (P3[26]/STCLK/MAT0[1]/PWM1[3]), JP20.2
SSEL1: IC1.63 (P0[16]/RXD1/SSEL0/SSEL), JP2.2
STP1: IC1.75 (P2[0]/PWM1[1]/TXD1), JP7.3; also elsewhere on the board
STP2: IC1.74 (P2[1]/PWM1[2]/RXD1), JP9.3; also elsewhere on the board
STP3: IC1.73 (P2[2]/PWM1[3]/CTS1/TRACEDATA[3]), JP12.3; also elsewhere on the board
STP4: IC1.70 (P2[3]/PWM1[4]/DCD1/TRACEDATA[2]), JP15.3; also elsewhere on the board
STP5: IC1.65 (P2[8]/TD2/TXD2); also elsewhere on the board
TH1: IC1.9 (P0[23]/AD0[0]/I2SRX_CLK/CAP3[0]); also elsewhere on the board
TH2: IC1.8 (P0[24]/AD0[1]/I2SRX_WS/CAP3[1]); also elsewhere on the board
TH3: IC1.7 (P0[25]/AD0[2]/I2SRX_SDA/TXD3); also elsewhere on the board
TH4: IC1.6 (P0[26]/AD0[3]/AOUT/RXD3); also elsewhere on the board
TX_0: IC1.98 (P0[2]/TXD0/AD0[7]), JP5.5
USB_D+: C5.2, IC1.29 (P0[29]/USB_D+), R7.1, R8.2
USB_D-: C4.2, IC1.30 (P0[30]/USB_D-), R9.2
VBB: JP17.1; also elsewhere on the board
VUSB: X14.VBUS; also elsewhere on the board
X_MAX: C79.1, IC1.39 (P1[25]/MC1A/MAT1[1]), R95.2
X_MIN: C78.1, IC1.38 (P1[24]/MCFB2/PWM1[5]/MOSI0), R92.2
Y_MAX: C81.1, IC1.43 (P1[27]/CLKOUT/USB_OVRCR/CAP0[1]), R99.2
Y_MIN: C80.1, IC1.40 (P1[26]/MC1B/PWM1[6]/CAP0[0]), R97.2
Z_MAX: C83.1, IC1.45 (P1[29]/MC2B/PCAP1[1]/MAT0[1]), R103.2
Z_MIN: C82.1, IC1.44 (P1[28]/MC2A/PCAP1[0]/MAT0[0]), R101.2

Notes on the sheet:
SD Card connector
UART0
(Also for ISP Loading)
http://smoothieware.org
Symbol reversed in Sparkfun
Smoothieboard
by: Arthur Wolf
produced by: Trinity Labs
Licensed under GPL: http://www.gnu.org/licenses/gpl.html
Thanks for the support and contributions of the Reprap Community

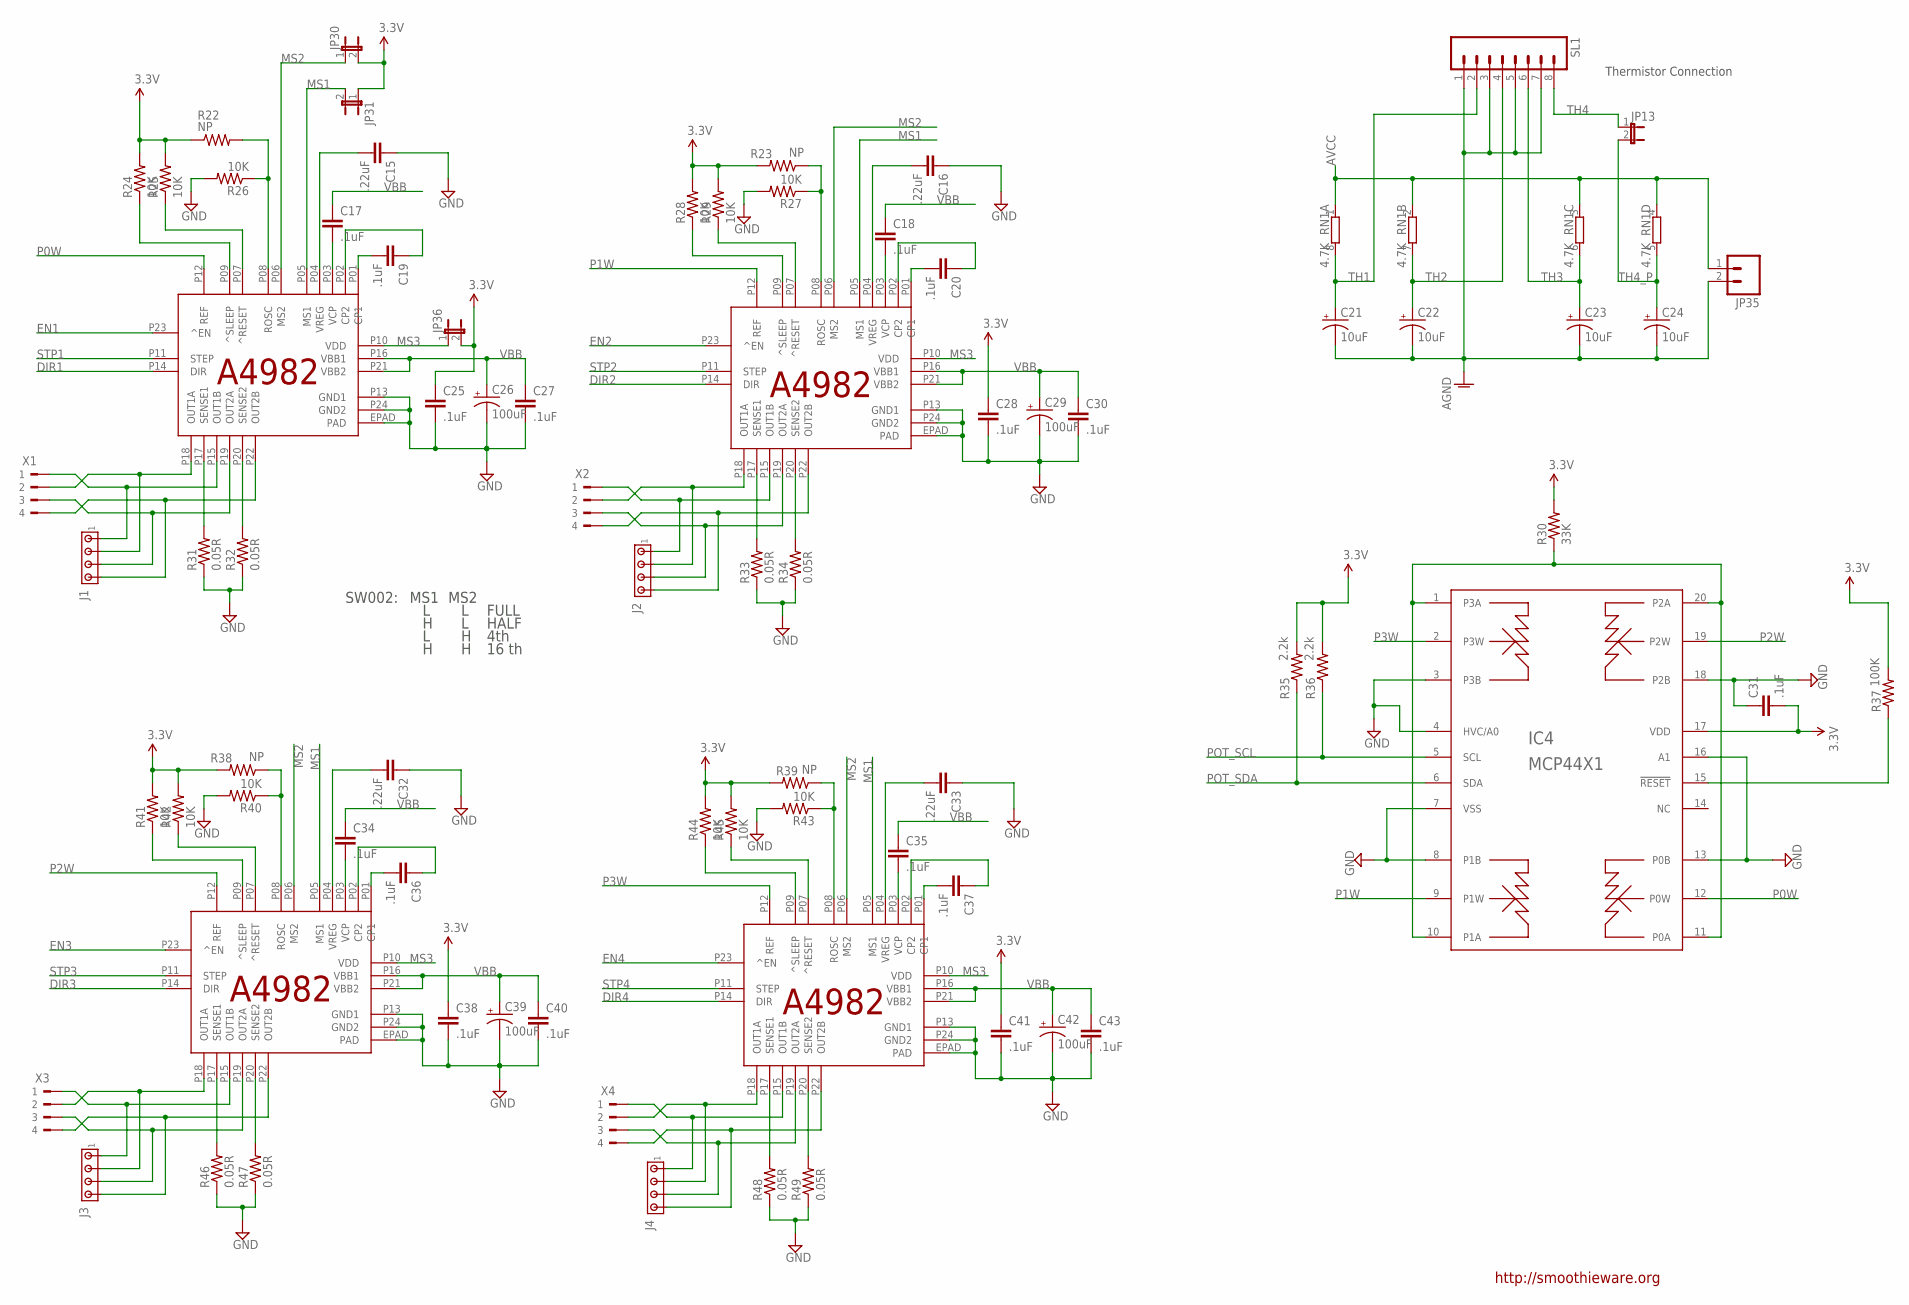
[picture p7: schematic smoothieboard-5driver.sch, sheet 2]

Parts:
C15, C16, C32, C33: .22uF; C0603
C17, C18, C19, C20, C25, C27, C28, C30, C31, C34, C35, C36, C37, C38, C40, C41, C43: .1uF; C0603
C21, C22, C23, C24: 10uF; EIA3216
C26, C29, C39, C42: 100uF; PANASONIC_E
IC2, IC3, IC5, IC6: A5984; ETSSOP24
IC4: MCP44X1; TSSOP20
J1, J2, J3, J4: MTA04-100; 10X04MTA
JP13, JP30, JP31, JP36: JUMPER-2SMD-NC; SJ_2S
JP35: M02PTH; 1X02
R22, R23, R38, R39: NP; R0603
R24, R25, R26, R27, R28, R29, R40, R41, R42, R43, R44, R45: 10K; R0603
R30: 33K; R0603
R31, R32, R33, R34, R46, R47, R48, R49: 0.05R; R2512
R35, R36: 2.2k; R0603
R37: 100K; R0603
RN1: 4.7K; 0603-ARV
SL1: M08; 08P
X1, X2, X3, X4: 180G-4

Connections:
3.3V: C25.1, C28.1, C31.2, C38.1, C41.1, IC4.17 (VDD), JP30.2, JP31.1, JP36.2, R22.1, R23.2, R24.2, R25.2, R28.2, R29.2, R30.2, R35.2, R36.2, R37.2, R38.2, R39.2, R41.2, R42.2, R44.2, R45.2; also elsewhere on the board
AGND: C21.C (-), C22.C (-), C23.C (-), C24.C (-), JP35.2, SL1.1, SL1.3, SL1.5, SL1.7; also elsewhere on the board
AVCC: JP35.1, RN1.1, RN1.2 (1), RN1.3 (1), RN1.4 (1); also elsewhere on the board
DIR1: IC2.P14 (DIR); also elsewhere on the board
DIR2: IC3.P14 (DIR); also elsewhere on the board
DIR3: IC5.P14 (DIR); also elsewhere on the board
DIR4: IC6.P14 (DIR); also elsewhere on the board
EN1: IC2.P23 (^EN); also elsewhere on the board
EN2: IC3.P23 (^EN); also elsewhere on the board
EN3: IC5.P23 (^EN); also elsewhere on the board
EN4: IC6.P23 (^EN); also elsewhere on the board
GND: C15.1, C16.1, C25.2, C26.-, C27.2, C28.2, C29.-, C30.2, C31.1, C32.1, C33.1, C38.2, C39.-, C40.2, C41.2, C42.-, C43.2, IC2.EPAD (PAD), IC2.P13 (GND1), IC2.P24 (GND2), IC3.EPAD (PAD), IC3.P13 (GND1), IC3.P24 (GND2), IC4.3 (P3B), IC4.4 (HVC/A0), IC4.7 (VSS), IC4.8 (P1B), IC4.13 (P0B), IC4.16 (A1), IC4.18 (P2B), IC5.EPAD (PAD), IC5.P13 (GND1), IC5.P24 (GND2), IC6.EPAD (PAD), IC6.P13 (GND1), IC6.P24 (GND2), R26.2, R27.2, R31.1, R32.1, R33.1, R34.1, R40.2, R43.2, R46.1, R47.1, R48.1, R49.1; also elsewhere on the board
MS1: IC2.P05 (MS1), IC3.P05 (MS1), IC5.P05 (MS1), IC6.P05 (MS1), JP31.2; also elsewhere on the board
MS2: IC2.P06 (MS2), IC3.P06 (MS2), IC5.P06 (MS2), IC6.P06 (MS2), JP30.1; also elsewhere on the board
MS3: IC2.P10 (VDD), IC3.P10 (VDD), IC5.P10 (VDD), IC6.P10 (VDD), JP36.1; also elsewhere on the board
unnamed: C20.2, IC3.P01 (CP1)
unnamed: C20.1, IC3.P02 (CP2)
unnamed: IC2.P07 (^RESET), R25.1
unnamed: C18.2, IC3.P03 (VCP)
unnamed: IC3.P17 (SENSE1), R33.2
unnamed: IC3.P20 (SENSE2), R34.2
unnamed: IC3.P18 (OUT1A), J2.2, X2.2
unnamed: IC3.P15 (OUT1B), J2.1, X2.1
unnamed: IC3.P19 (OUT2A), J2.3, X2.3
unnamed: IC4.15 (!RESET), R37.1
unnamed: IC3.P22 (OUT2B), J2.4, X2.4
unnamed: IC4.1 (P3A), IC4.10 (P1A), IC4.11 (P0A), IC4.20 (P2A), R30.1
unnamed: IC3.P08 (ROSC), R23.1, R27.1
unnamed: C16.2, IC3.P04 (VREG)
unnamed: IC3.P09 (^SLEEP), R28.1
unnamed: C36.2, IC5.P01 (CP1)
unnamed: C36.1, IC5.P02 (CP2)
unnamed: C34.2, IC5.P03 (VCP)
unnamed: IC5.P17 (SENSE1), R46.2
unnamed: IC5.P20 (SENSE2), R47.2
unnamed: IC5.P18 (OUT1A), J3.2, X3.2
unnamed: IC5.P15 (OUT1B), J3.1, X3.1
unnamed: IC5.P19 (OUT2A), J3.3, X3.3
unnamed: IC5.P22 (OUT2B), J3.4, X3.4
unnamed: IC3.P07 (^RESET), R29.1
unnamed: IC5.P07 (^RESET), R42.1
unnamed: IC5.P08 (ROSC), R38.1, R40.1
unnamed: C32.2, IC5.P04 (VREG)
unnamed: IC6.P07 (^RESET), R45.1
unnamed: IC5.P09 (^SLEEP), R41.1
unnamed: C37.2, IC6.P01 (CP1)
unnamed: C37.1, IC6.P02 (CP2)
unnamed: C35.2, IC6.P03 (VCP)
unnamed: IC6.P17 (SENSE1), R48.2
unnamed: IC6.P20 (SENSE2), R49.2
unnamed: IC6.P15 (OUT1B), J4.1, X4.1
unnamed: IC6.P19 (OUT2A), J4.3, X4.3
unnamed: IC6.P22 (OUT2B), J4.4, X4.4
unnamed: IC6.P08 (ROSC), R39.1, R43.1
unnamed: C33.2, IC6.P04 (VREG)
unnamed: IC6.P09 (^SLEEP), R44.1
unnamed: IC6.P18 (OUT1A), J4.2, X4.2
unnamed: C19.2, IC2.P01 (CP1)
unnamed: C19.1, IC2.P02 (CP2)
unnamed: C17.2, IC2.P03 (VCP)
unnamed: IC2.P17 (SENSE1), R31.2
unnamed: IC2.P20 (SENSE2), R32.2
unnamed: IC2.P18 (OUT1A), J1.2, X1.2
unnamed: IC2.P15 (OUT1B), J1.1, X1.1
unnamed: IC2.P19 (OUT2A), J1.3, X1.3
unnamed: IC2.P22 (OUT2B), J1.4, X1.4
unnamed: IC2.P08 (ROSC), R22.2, R26.1
unnamed: C15.2, IC2.P04 (VREG)
unnamed: IC2.P09 (^SLEEP), R24.1
P0W: IC2.P12 (REF), IC4.12 (P0W)
P1W: IC3.P12 (REF), IC4.9 (P1W)
P2W: IC4.19 (P2W), IC5.P12 (REF)
P3W: IC4.2 (P3W), IC6.P12 (REF)
POT_SCL: IC4.5 (SCL), R36.1; also elsewhere on the board
POT_SDA: IC4.6 (SDA), R35.1; also elsewhere on the board
STP1: IC2.P11 (STEP); also elsewhere on the board
STP2: IC3.P11 (STEP); also elsewhere on the board
STP3: IC5.P11 (STEP); also elsewhere on the board
STP4: IC6.P11 (STEP); also elsewhere on the board
TH1: C21.A (+), RN1.8 (2), SL1.2; also elsewhere on the board
TH2: C22.A (+), RN1.7 (2), SL1.4; also elsewhere on the board
TH3: C23.A (+), RN1.6 (2), SL1.6; also elsewhere on the board
TH4: JP13.1, SL1.8; also elsewhere on the board
TH4_P: C24.A (+), JP13.2, RN1.5 (2)
VBB: C17.1, C18.1, C26.+, C27.1, C29.+, C30.1, C34.1, C35.1, C39.+, C40.1, C42.+, C43.1, IC2.P16 (VBB1), IC2.P21 (VBB2), IC3.P16 (VBB1), IC3.P21 (VBB2), IC5.P16 (VBB1), IC5.P21 (VBB2), IC6.P16 (VBB1), IC6.P21 (VBB2); also elsewhere on the board

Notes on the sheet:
SW002:
MS1
MS2
FULL
HALF
4th
16 th
Thermistor Connection
http://smoothieware.org

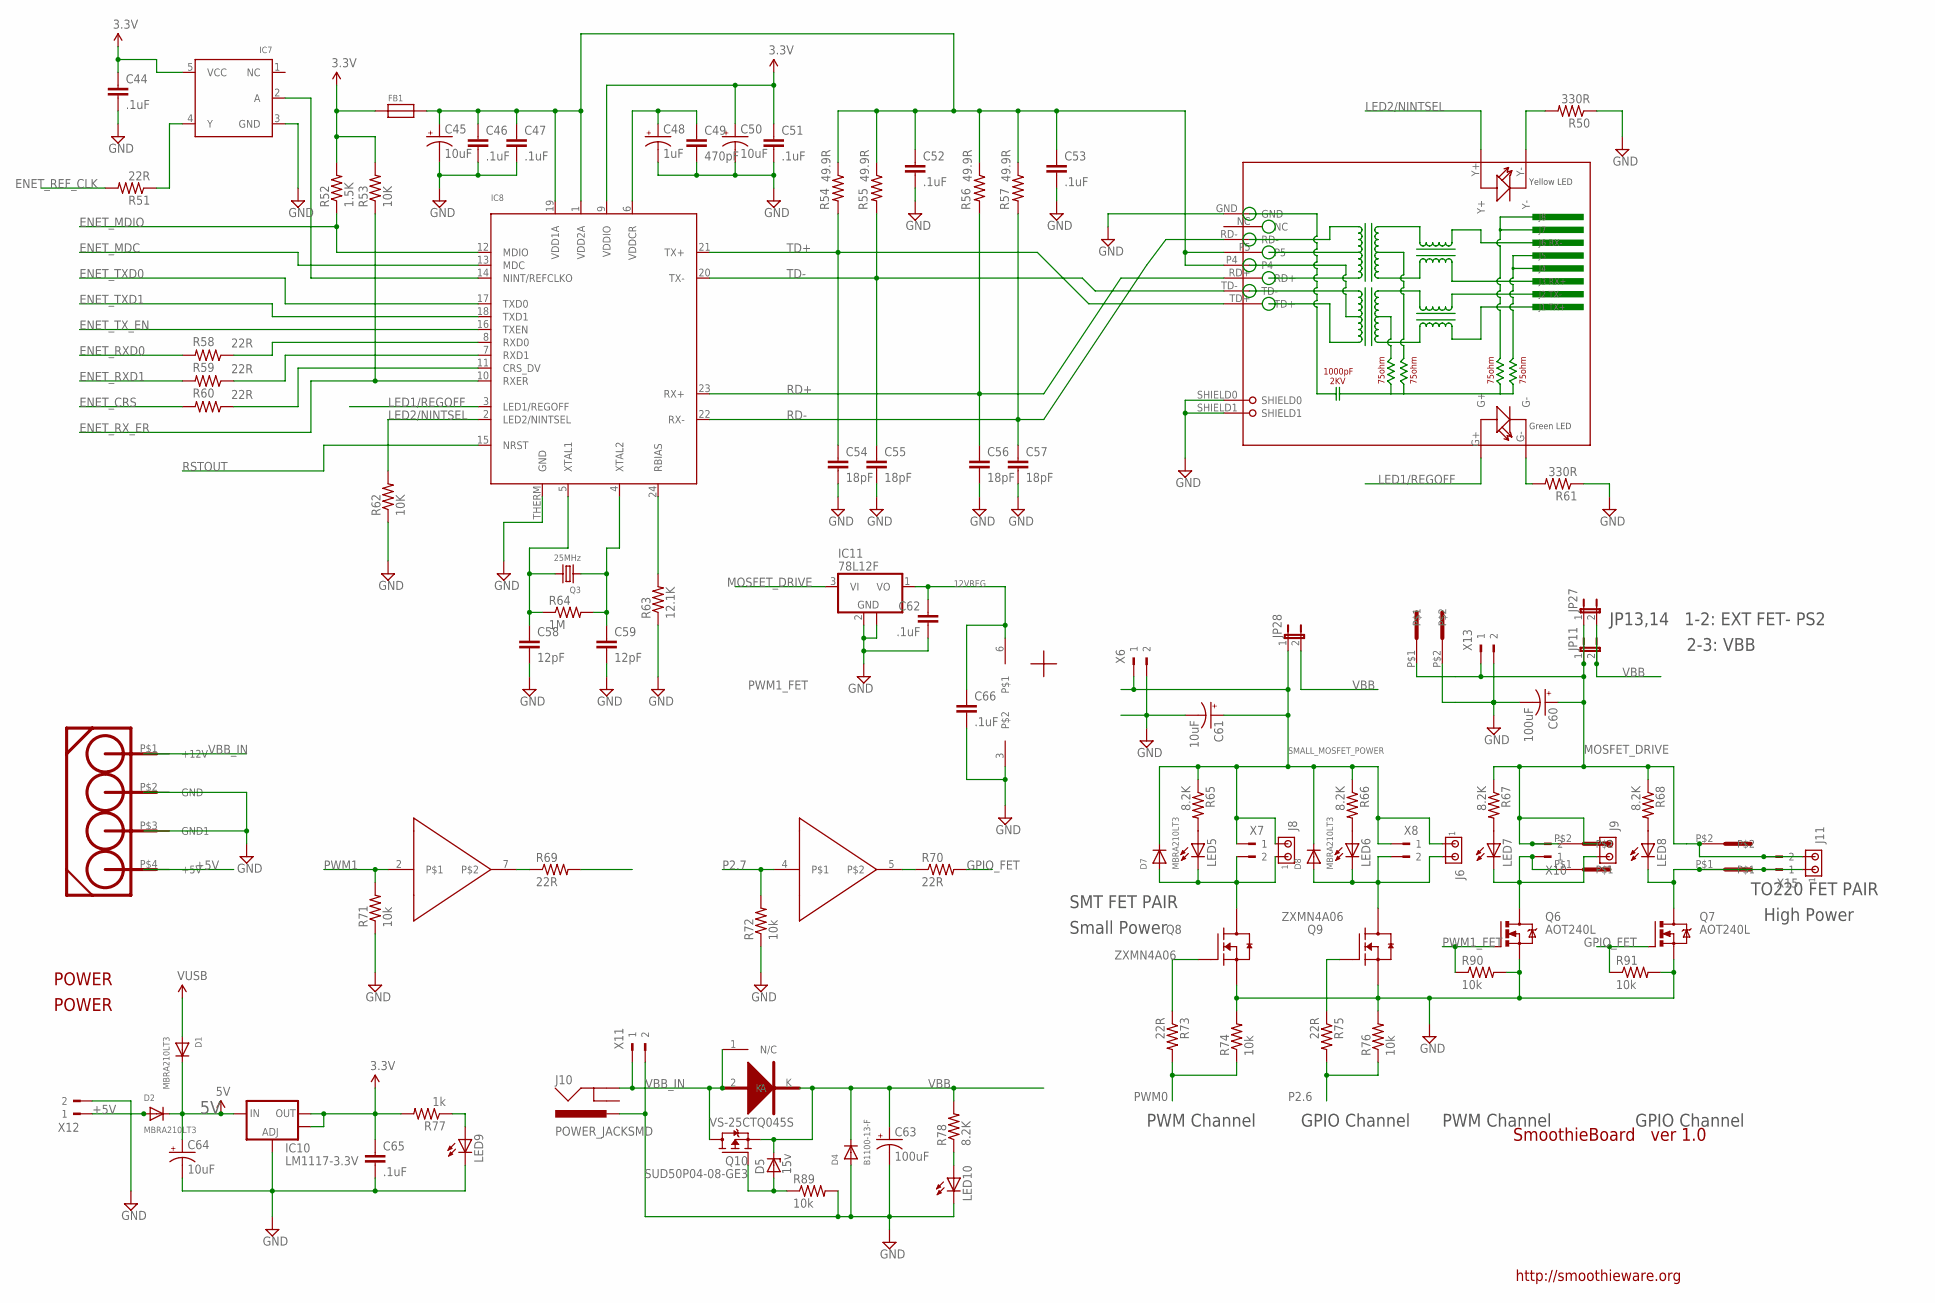
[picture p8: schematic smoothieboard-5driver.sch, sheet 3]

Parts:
C44, C46, C47, C51, C52, C53, C62, C65, C66: .1uF; C0603
C45, C50, C61, C64: 10uF; EIA3216
C48: 1uF; EIA3216
C49: 470pF; C0603K
C54, C55, C56, C57: 18pF; C0603
C58, C59: 12pF; C0603
C60, C63: 100uF; PANASONIC_E
D1, D2, D7, D8: MBRA210LT3; SMADIODE
D3: VS-25CTQ045S; TO263AB
D4: B1100-13-F; SMADIODE
D5: 15v; SMB
FB1: FERRITE; 0603
IC7: 74LVC1G04; SOT23-5
IC8: LAN8720; QFN24_4MM
IC10: LM1117-3.3V; SOT223
IC11: 78L12F; SOT89
IC14: TC4427; SOIC8
J6, J8, J9, J11: MTA02-100; 10X02MTA
J10: POWER_JACKSMD; POWER_JACK_SMD
JP11, JP27, JP28: JP1E; JP1
LED5, LED6, LED7, LED8, LED9, LED10: LEDCHIP-LED0805; CHIP-LED0805
POWER: POWER; MOLEX8981
Q3: 25MHz; CRYSTAL_3.2X2.5
Q6, Q7: AOT240L; TO220BV
Q8, Q9: ZXMN4A06; SOT230P700X160-4N
Q10: SUD50P04-08-GE3; TO252
R50, R61: 330R; R0603
R51, R58, R59, R60, R69, R70, R73, R75: 22R; R0603
R52: 1.5K; R0603
R53, R62: 10K; R0603
R54, R55, R56, R57: 49.9R; R0603
R63: 12.1K; R0603
R64: 1M; R0603
R65, R66, R67, R68, R78: 8.2K; R0603
R71, R72, R74, R76, R89, R90, R91: 10k; R0603
R77: 1k; R0603
RJ1: HR911105A
U$5, U$6, U$10: 5MMCONN; 1715250000
X6, X7, X8, X10, X11, X12, X13, X15: 180G-2

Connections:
3.3V: C44.1, C50.A (+), C51.1, C65.1, FB1.1, IC7.5 (VCC), IC8.9 (VDDIO), IC10.2 (OUT), IC10.4 (OUT), R52.2, R53.2, R77.2; also elsewhere on the board
5V: C64.A (+), D1.C, D2.C, IC10.3 (IN); also elsewhere on the board
12VREG: C62.1, C66.1, IC11.1 (VO), IC14.6; also elsewhere on the board
+5V: D2.A, POWER.P$4 (+5V), X12.1
ENET_CRS: R60.2; also elsewhere on the board
ENET_MDC: IC8.13 (MDC); also elsewhere on the board
ENET_MDIO: IC8.12 (MDIO), R52.1; also elsewhere on the board
ENET_REF_CLK: R51.2; also elsewhere on the board
ENET_RXD0: R58.2; also elsewhere on the board
ENET_RXD1: R59.2; also elsewhere on the board
ENET_RX_ER: IC8.10 (RXER), R53.1; also elsewhere on the board
ENET_TXD0: IC8.17 (TXD0); also elsewhere on the board
ENET_TXD1: IC8.18 (TXD1); also elsewhere on the board
ENET_TX_EN: IC8.16 (TXEN); also elsewhere on the board
GND: C44.2, C45.C (-), C46.2, C47.2, C48.C (-), C49.2, C50.C (-), C51.2, C52.2, C53.2, C54.2, C55.2, C56.2, C57.2, C58.2, C59.2, C60.-, C61.C (-), C62.2, C63.-, C64.C (-), C65.2, C66.2, D4.A, IC7.3 (GND), IC8.THERM (GND), IC10.1 (ADJ), IC11.2 (GND), IC11.2@1 (GND), IC14.3, J10.VIN0 (PWR), LED9.C, LED10.C, POWER.P$2 (GND), POWER.P$3 (GND1), Q6.S, Q7.S, Q8.3 (S), Q9.3 (S), R50.1, R61.1, R62.1, R63.1, R71.1, R72.1, R74.2, R76.2, R89.2, R90.2, R91.2, RJ1.GND, RJ1.SHIELD0, RJ1.SHIELD1, U$5.P$2, X6.2, X11.2, X12.2, X13.2; also elsewhere on the board
GPIO_FET: Q7.G, R70.2, R91.1
LED1/REGOFF: IC8.3 (LED1/REGOFF), RJ1.G+
LED2/NINTSEL: IC8.2 (LED2/NINTSEL), R62.2, RJ1.Y+
MOSFET_DRIVE: C60.+, IC11.3 (VI), J9.2, J11.2, JP11.1, JP27.1, R67.1, R68.1, U$5.P$1, U$6.P$2, U$10.P$2, X10.2, X13.1, X15.2
unnamed: IC14.7, R69.1
unnamed: LED10.A, R78.1
unnamed: D8.A, J6.2, LED6.C, Q9.4 (D), X8.2
unnamed: IC14.5, R70.1
unnamed: R61.2, RJ1.G-
unnamed: C45.A (+), C46.1, C47.1, C52.1, C53.1, FB1.2, IC8.1 (VDD2A), IC8.19 (VDD1A), R54.1, R55.1, R56.1, R57.1, RJ1.P4, RJ1.P5
unnamed: IC8.8 (RXD0), R58.1
unnamed: R50.2, RJ1.Y-
unnamed: IC8.7 (RXD1), R59.1
unnamed: IC8.11 (CRS_DV), R60.1
unnamed: C59.1, IC8.4 (XTAL2), Q3.1, R64.2
unnamed: C58.1, IC8.5 (XTAL1), Q3.2, R64.1
unnamed: IC8.24 (RBIAS), R63.2
unnamed: Q8.1 (G), R73.1
unnamed: Q9.1 (G), R75.1
unnamed: IC7.2 (A), IC8.14 (NINT/REFCLKO)
unnamed: IC7.4 (Y), R51.1
unnamed: LED9.A, R77.1
unnamed: LED5.A, R65.2
unnamed: C48.A (+), C49.1, IC8.6 (VDDCR)
unnamed: D7.A, J8.1, LED5.C, Q8.4 (D), X7.2
unnamed: LED6.A, R66.2
unnamed: J9.1, LED7.C, Q6.D, U$10.P$1, X10.1
unnamed: J11.1, LED8.C, Q7.D, U$6.P$1, X15.1
unnamed: LED7.A, R67.2
unnamed: D5.A, Q10.1 (G), R89.1
unnamed: LED8.A, R68.2
P2.6: R75.2, R76.1; also elsewhere on the board
P2.7: IC14.4, R72.2; also elsewhere on the board
PWM0: R73.2, R74.1; also elsewhere on the board
PWM1: IC14.2, R71.2; also elsewhere on the board
PWM1_FET: Q6.G, R69.2, R90.1
RD+: C56.1, IC8.23 (RX+), R56.2, RJ1.RD+
RD-: C57.1, IC8.22 (RX-), R57.2, RJ1.RD-
RSTOUT: IC8.15 (NRST); also elsewhere on the board
SMALL_MOSFET_POWER: C61.A (+), D7.C, D8.C, J6.1, J8.2, JP28.1, R65.1, R66.1, X6.1, X7.1, X8.1
TD+: C54.1, IC8.21 (TX+), R54.2, RJ1.TD+
TD-: C55.1, IC8.20 (TX-), R55.2, RJ1.TD-
VBB: C63.+, D3.K, D4.C, D5.C, JP11.2, JP27.2, JP28.2, Q10.2 (S), R78.2; also elsewhere on the board
VBB_IN: D3.1 (N/C), D3.2 (A), J10.P$4 (GND), POWER.P$1 (+12V), Q10.3 (D), X11.1
VUSB: D1.A; also elsewhere on the board

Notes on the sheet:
JP13,14 1-2: EXT FET- PS2
2-3: VBB
SMT FET PAIR
Small Power
TO220 FET PAIR
High Power
PWM Channel
GPIO Channel
SmoothieBoard ver 1.0
http://smoothieware.org
VS-25CTQ045S

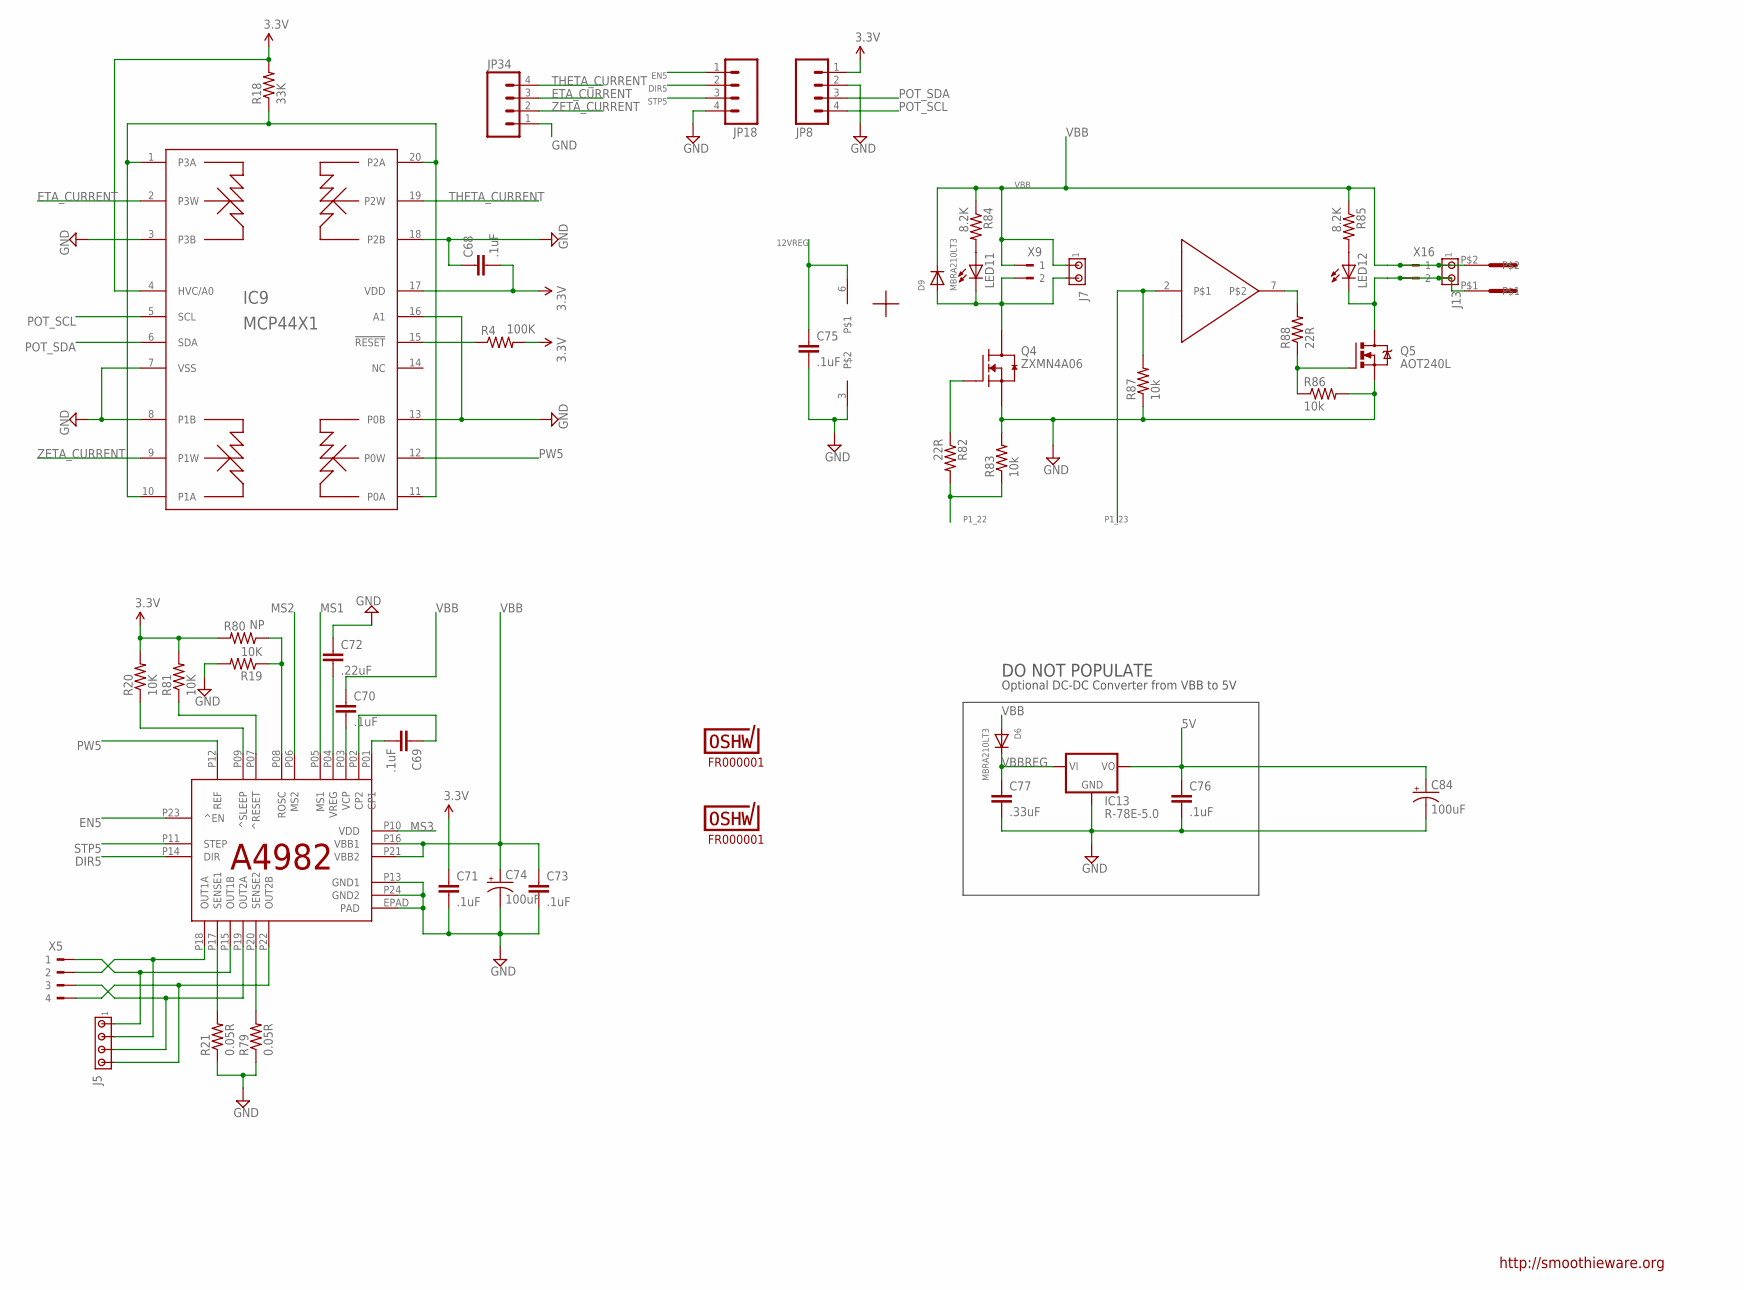
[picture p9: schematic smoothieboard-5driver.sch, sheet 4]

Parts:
C68, C69, C70, C71, C73, C75, C76: .1uF; C0603
C72: .22uF; C0603
C74: 100uF; PANASONIC_E
C77: .33uF; C0603
C84: 100uF; PANASONIC_D
D6, D9: MBRA210LT3; SMADIODE
IC9: MCP44X1; TSSOP20
IC12: A5984; ETSSOP24
IC13: R-78E-5.0; R-78
IC15: TC4427; SOIC8
J5: MTA04-100; 10X04MTA
J7, J13: MTA02-100; 10X02MTA
JP8, JP18, JP34: M041X04_NO_SILK; 1X04_NO_SILK
LED11, LED12: LEDCHIP-LED0805; CHIP-LED0805
Q4: ZXMN4A06; SOT230P700X160-4N
Q5: AOT240L; TO220BV
R4: 100K; R0603
R18: 33K; R0603
R19, R20, R81: 10K; R0603
R21, R79: 0.05R; R2512
R80: NP; R0603
R82, R88: 22R; R0603
R83, R86, R87: 10k; R0603
R84, R85: 8.2K; R0603
U$7: 5MMCONN; 1715250000
U$11: FR000001; CERT-SMALL-SILK
U$12: FR000001; CERT-MED-SILK
X5: 180G-4
X9, X16: 180G-2

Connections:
3.3V: C68.2, C71.1, IC9.4 (HVC/A0), IC9.17 (VDD), JP8.1, R4.2, R18.2, R20.2, R80.2, R81.2; also elsewhere on the board
5V: C76.1, C84.+, IC13.3 (VO); also elsewhere on the board
12VREG: C75.1, IC15.6; also elsewhere on the board
DIR5: IC12.P14 (DIR), JP18.2; also elsewhere on the board
EN5: IC12.P23 (^EN), JP18.1; also elsewhere on the board
ETA_CURRENT: IC9.2 (P3W), JP34.3
GND: C68.1, C71.2, C72.1, C73.2, C74.-, C75.2, C76.2, C77.2, C84.-, IC9.3 (P3B), IC9.7 (VSS), IC9.8 (P1B), IC9.13 (P0B), IC9.16 (A1), IC9.18 (P2B), IC12.EPAD (PAD), IC12.P13 (GND1), IC12.P24 (GND2), IC13.2 (GND), IC15.3, JP8.2, JP18.4, JP34.1, Q4.3 (S), Q5.S, R19.2, R21.1, R79.1, R83.2, R86.2, R87.1; also elsewhere on the board
GPIO_FET1: Q5.G, R86.1, R88.1
MS1: IC12.P05 (MS1); also elsewhere on the board
MS2: IC12.P06 (MS2); also elsewhere on the board
MS3: IC12.P10 (VDD); also elsewhere on the board
unnamed: IC9.15 (!RESET), R4.1
unnamed: D9.A, J7.2, LED11.C, Q4.4 (D), X9.2
unnamed: IC9.1 (P3A), IC9.10 (P1A), IC9.11 (P0A), IC9.20 (P2A), R18.1
unnamed: C69.2, IC12.P01 (CP1)
unnamed: C69.1, IC12.P02 (CP2)
unnamed: C70.2, IC12.P03 (VCP)
unnamed: IC12.P17 (SENSE1), R21.2
unnamed: IC12.P20 (SENSE2), R79.2
unnamed: IC12.P18 (OUT1A), J5.2, X5.2
unnamed: IC12.P15 (OUT1B), J5.1, X5.1
unnamed: IC12.P19 (OUT2A), J5.3, X5.3
unnamed: IC12.P22 (OUT2B), J5.4, X5.4
unnamed: IC12.P08 (ROSC), R19.1, R80.1
unnamed: C72.2, IC12.P04 (VREG)
unnamed: IC12.P09 (^SLEEP), R20.1
unnamed: IC12.P07 (^RESET), R81.1
unnamed: Q4.1 (G), R82.1
unnamed: LED11.A, R84.2
unnamed: J13.2, LED12.C, Q5.D, U$7.P$1, X16.2
unnamed: LED12.A, R85.2
unnamed: IC15.7, R88.2
P1_22: R82.2, R83.1; also elsewhere on the board
P1_23: IC15.2, R87.2; also elsewhere on the board
POT_SCL: IC9.5 (SCL), JP8.4; also elsewhere on the board
POT_SDA: IC9.6 (SDA), JP8.3; also elsewhere on the board
PW5: IC9.12 (P0W), IC12.P12 (REF)
STP5: IC12.P11 (STEP), JP18.3; also elsewhere on the board
THETA_CURRENT: IC9.19 (P2W), JP34.4
VBB: C70.1, C73.1, C74.+, D6.A, D9.C, IC12.P16 (VBB1), IC12.P21 (VBB2), J7.1, J13.1, R84.1, R85.1, U$7.P$2, X9.1, X16.1; also elsewhere on the board
VBBREG: C77.1, D6.C, IC13.1 (VI)
ZETA_CURRENT: IC9.9 (P1W), JP34.2

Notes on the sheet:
http://smoothieware.org
DO NOT POPULATE
Optional DC-DC Converter from VBB to 5V

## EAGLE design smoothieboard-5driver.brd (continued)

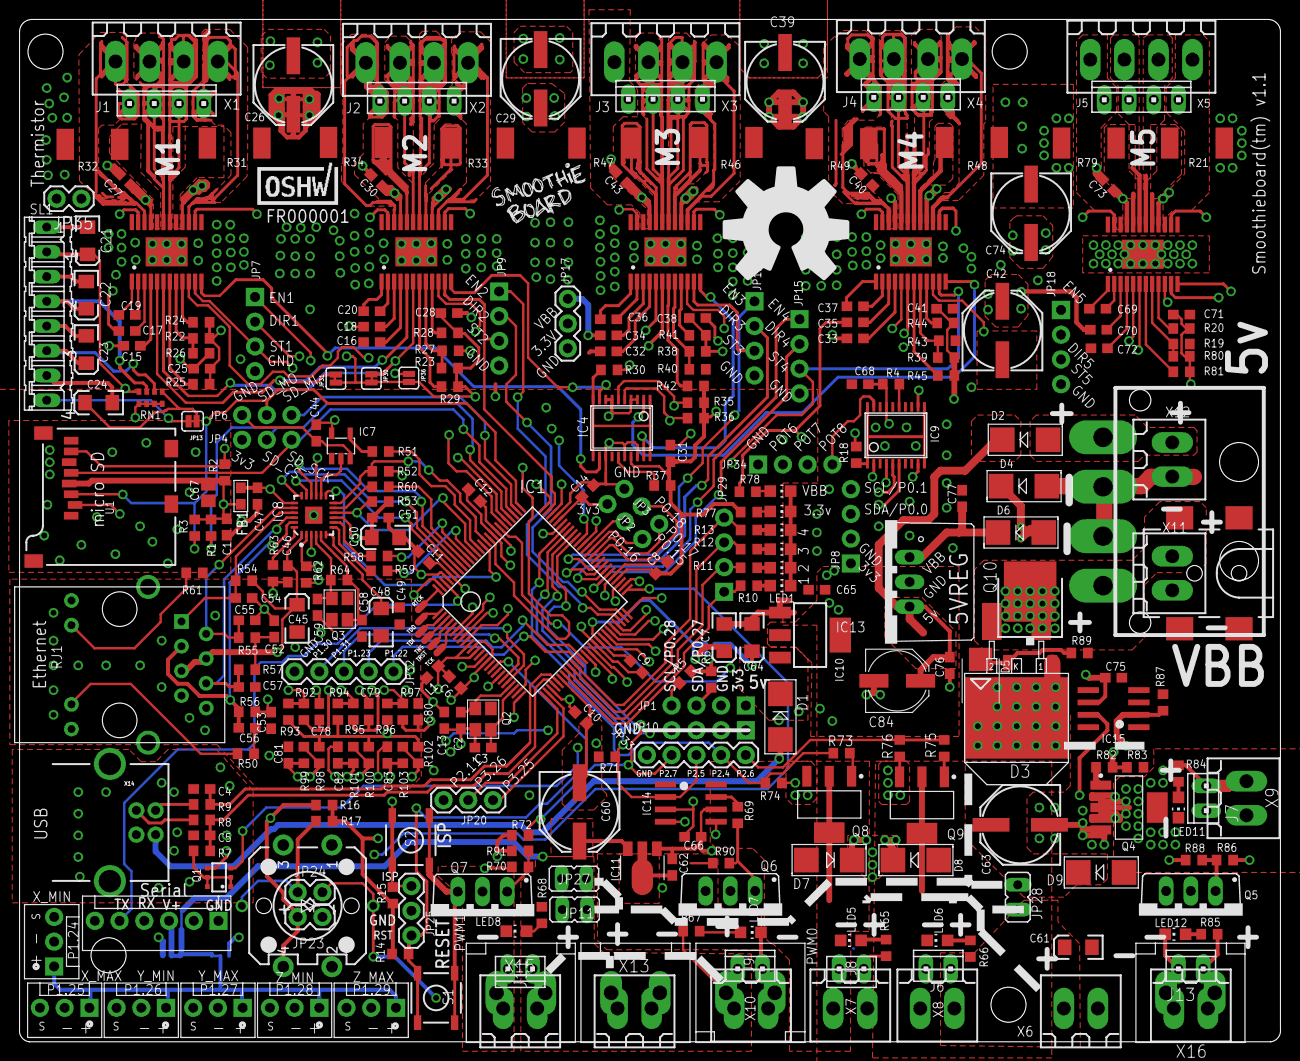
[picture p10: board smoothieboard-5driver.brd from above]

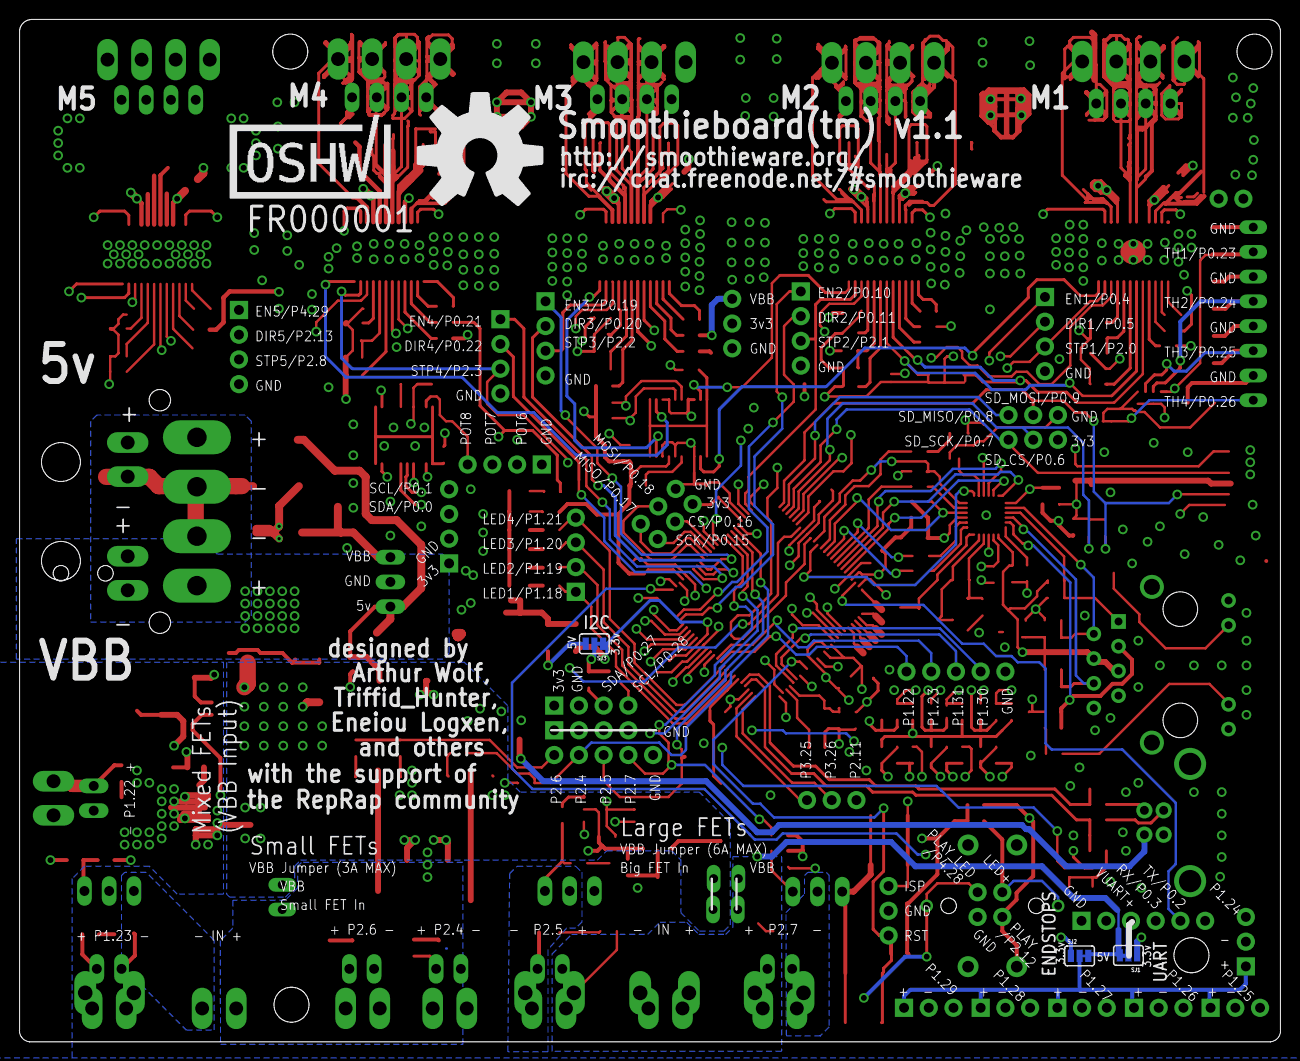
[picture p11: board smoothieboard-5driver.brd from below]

Board: 4 copper layers, 129.6 x 105.0 mm, 318 parts (5 on the bottom side), 227 nets.

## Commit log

2012-12-23 initial commit of eagle files
    [smoothieboard.brd, smoothieboard.sch]
2013-01-09 Added USB-B Connector, other fixes
    [smoothieboard.brd, smoothieboard.sch]
2013-01-09 Routed SD card ground directly to ground plane
    [smoothieboard.brd]
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2013-01-09 lots of board cleanup:
    removed thermals on high currenta ares
    HEAPS of trace simplification
    shrink 3v3 plane, use space for other signals
    bulk up many polygons, use ranks to prevent shorts
    separate analog ground, connect thermistors to AVCC/AGND
    make trace angles 45 degrees
    broken polygons connected
    heaps of other fixes
    changes to schematic:
    thermistors connected to AGND/AVCC
    [smoothieboard.brd, smoothieboard.sch]
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2013-01-09 give main IC value of LPC1769 to ease BOM generation
    [smoothieboard.brd, smoothieboard.sch]
2013-01-09 switch 78L12Z for 78L12F surface mount package. also route remaining ratsnest wires- all were traces contacting pad, just not connected to center of pad
    [smoothieboard.brd, smoothieboard.sch]
2013-01-09 USB-B connector, solder jumper for 5v/3v3 UART power (NOT signals, they're always 3v3)
    [smoothieboard.brd, smoothieboard.sch]
2013-01-09 switch USB CONNECT transistor for a FET, move UART voltage selector next to UART header
    [smoothieboard.brd, smoothieboard.sch]
2013-01-09 5v trace was grazing one of the uart pins
    [smoothieboard.brd]
2013-01-10 Added polarity mark for TC4427 manually
    [smoothieboard.brd]
2013-01-10 Moved C34 to allow heatsink to reach all four drivers from side
    [smoothieboard.brd]
2013-01-10 Fixed I2C Header Spacing
    [smoothieboard.brd]
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2013-01-10 Added thermal relief to large caps
    [smoothieboard.brd]
2013-01-10 Removed Mosfet Driver Power SMD Jack
    [smoothieboard.brd, smoothieboard.sch]
2013-01-10 Removed second ground connection from IC11 (to improve MOSFET_DRIVE trace current handling)
    [smoothieboard.brd]
2013-01-10 Fixed MOSFET labels on schematic to match BOM
    [smoothieboard.brd, smoothieboard.sch]
2013-01-10 Changed 78L05 from to-92 to sot-89 in bom, updated USB connector in BOM
    [bom.xls]
2013-01-14 Changed Heated Bed connectors
    [smoothieboard.brd, smoothieboard.sch]
2013-03-20 Cloned 4driver board to 5driver in preparation for future work. No changes to board yet
    [smoothieboard-4driver.brd, smoothieboard-4driver.sch, smoothieboard-5driver.brd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]
2013-03-20 Added 5th driver, 2nd digipot. Still lots of layout work to do
    [smoothieboard-5driver.brd, smoothieboard-5driver.sch]
2013-03-23 shifted power connectors, lots of rearranging, still more to do
    [smoothieboard-5driver.brd, smoothieboard-5driver.sch]
2013-03-23 added 1x4 connector for 5th driver en/dir/step signals to match other drivers
    [smoothieboard-5driver.brd, smoothieboard-5driver.sch]
2013-03-24 Routing complete, DRC passes, now time for fine tuning
    [smoothieboard-5driver.brd]
2013-03-24 remove VBB poly supplying mosfet drivers from bottom of board to improve driver heatsinking, VBB poly on route15 is adequate.
    [smoothieboard-5driver.brd]
2013-03-24 Gave small mosfets more heatsink area, moved some signal traces from bottom layer to route15 to improve stepper driver cooling, lots of other tweaks
    [smoothieboard-5driver.brd, smoothieboard-5driver.sch]
2013-03-24 Added a bunch of ground stitching vias, also some routing tweaks
    [smoothieboard-5driver.brd]
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2013-03-31 use thermal vias to improve heatsinking for Q4 (small mosfet #3)
    [smoothieboard-5driver.brd]
2013-03-31 Improve ground plane beneath uC by moving a bunch of traces around
    [smoothieboard-5driver.brd]
2013-04-01 Change type of primary diode to a more robust type with lower Vf, add a helper diode to prevent damage from primary diode's higher reverse leakage
    [smoothieboard-5driver.brd, smoothieboard-5driver.sch]
2013-04-01 Alternative reverse polarity protection using a P-MOSFET. Do not populate both P-MOSFET and Diode footprints, the parts overlap
    [smoothieboard-5driver.brd, smoothieboard-5driver.sch]
2013-04-02 add some heatsinking for reverse polarity mosfet on back of board using thermal vias
    [smoothieboard-5driver.brd, smoothieboard-5driver.sch]
2013-04-02 Silkscreen text added- M5, VBB, +5v etc part names adjusted Q8 and Q9 aligned 3.5mm footprints added to new mosfets and power input JP32/33 added with ground pins plus necessary rerouting C40 changed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
    probably other misc tweaks and fixes
    [smoothieboard-5driver.brd, smoothieboard-5driver.sch]
2013-04-02 move FTDI voltage selection solder jumper to bottom layer
    [smoothieboard-5driver.brd]
2013-04-02 move name silk for D3 to better position
    [smoothieboard-5driver.brd]
2013-04-02 added footprint for optional R-78E-5.0 dc-dc converter for converting from VBB to 5V
    [smoothieboard-5driver.brd, smoothieboard-5driver.sch]
2013-04-03 add pull-downs on large mosfet gates, tons of silkscreen tidying including labelling of signals in connectors and power routing indicators
    [smoothieboard-5driver.brd, smoothieboard-5driver.sch]
2013-04-11 UART voltage selector- add trace to select 5v by default, user must cut trace to select 3.3v
    [smoothieboard-5driver.brd]
2013-04-11 ensure all connectors include a 3.5mm footprint, remove 0.1" footprint from high current connector, minor routing updates
    [smoothieboard-5driver.brd, smoothieboard-5driver.sch]
2013-04-11 add solder pads for JTAG- not enough room to route a proper connector
    [smoothieboard-5driver.brd]
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2013-04-12 Break out digipot I2C bus to a header
    [smoothieboard-5driver.brd, smoothieboard-5driver.sch]
2013-04-12 add jumper for VBB power to new mosfets
    [smoothieboard-5driver.brd, smoothieboard-5driver.sch]
2013-04-22 Add solder jumper for endstop voltage selection, move labels to _tsilk layer instead of tnames
    [smoothieboard-5driver.brd, smoothieboard-5driver.sch]
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2013-04-29 Smash, move and resize names for endstop protection components
    [smoothieboard-5driver.brd]
2013-05-01 Move a couple of names off pads, short solder jumpers for x16 microstep by default, ensure A4982's thermal pads have tStop
    [smoothieboard-5driver.brd, smoothieboard-5driver.sch]
2013-07-07 Updated R-78 footprint, i2c V select, orientation marker to ic15, silk updates
    [smoothieboard-5driver.brd, smoothieboard-5driver.sch]
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2013-10-13 fix endstop input ESD protection
    [smoothieboard-5driver.brd, smoothieboard-5driver.sch]
2013-10-14 final fixes for test run of sbc
    [smoothieboard-5driver.brd]
2013-11-25 remove errant fragments of stop mask, reinstate approved DRC errors
    [smoothieboard-5driver.brd]
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2014-05-19 spaced out endstops and corrected sdcard spi header
    [smoothieboard-5driver.brd]
2014-05-19 updated irc url to chat.freenode.net (irc.freenode.net does not work anymore)
    [smoothieboard-5driver.brd]
2014-05-19 lots of silk including pinouts on the bottom
    [smoothieboard-5driver.brd, smoothieboard-5driver.sch]
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2014-06-16 added a touch of extra space between C1 and R1
    [smoothieboard-5driver.brd]
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2016-12-30 Update to v1.1
    Board updated to v1.1. Also added changelog.txt and other some other
    files needed for more complete license compliance.
    [smoothieboard-5driver.brd, smoothieboard-5driver.sch]
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

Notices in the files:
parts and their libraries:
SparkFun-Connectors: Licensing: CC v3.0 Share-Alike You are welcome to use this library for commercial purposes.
